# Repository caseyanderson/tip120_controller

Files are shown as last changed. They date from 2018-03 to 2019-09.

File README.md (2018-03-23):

# tip120_controller
Casey Anderson, 2018

## Overview

This repository provides `Printed Circuit Board` (`PCB`) files, as well as software examples, for an Arduino-based `TIP120` actuator controlled via `Potentiometer` (or any `Voltage Divider`). As described (in more detail) [here](http://bildr.org/2011/03/high-power-control-with-arduino-and-tip120/), the `TIP120` is capable of actuating a variety of devices including brushless DC motors, vibration motors, solenoids, and lightbulbs.

## PCB

This double-sided `Pin Through Hole` (`PTH`) PCB was created in EAGLE.

`VCC` is supplied to the `Arduino Mini` via `RAW` (12V maximum). `VCC` is also passed to the `T` pin of the `CONN JACK STEREO 3.5MM`. Connection to motors/solenoids/whatever is accomplished via 3.5mm audio cable. Rate of actuation is set via `Potentiometer` and passed to `Arduino Mini` via `A0`.

### BOM

Note: items without a `Manufacturer Part Number` are generic.

* 1x Arduino Pro Mini (3.3V, 8MHz)
* 1x SWITCH SLIDE SPDT 200MA 30V, `EG1218`
* 1x CONN PWR JACK 2X5.5MM SOLDER, `PJ-102A`
* 1x CONN JACK STEREO 3.5MM, `SJ1-3523N`
* 1x POT 10kR 1/20W CARBON LOG, `PTV09A-4020F-A103`
* 1x TIP120
* 1x 1N4004 Diode
* 1x 220R
* 1x 2.2kR
* 1x 5mm LED
* 1x Motor/Solenoid/Light

### Photo

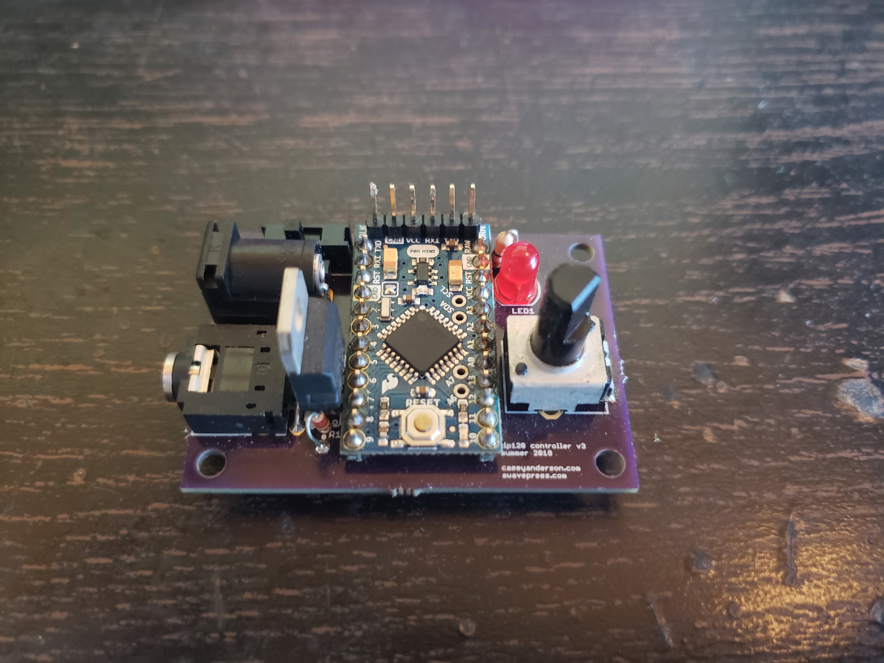
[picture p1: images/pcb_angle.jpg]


## SOFTWARE

Currently only the absolute simplest example of PWM. More to follow.

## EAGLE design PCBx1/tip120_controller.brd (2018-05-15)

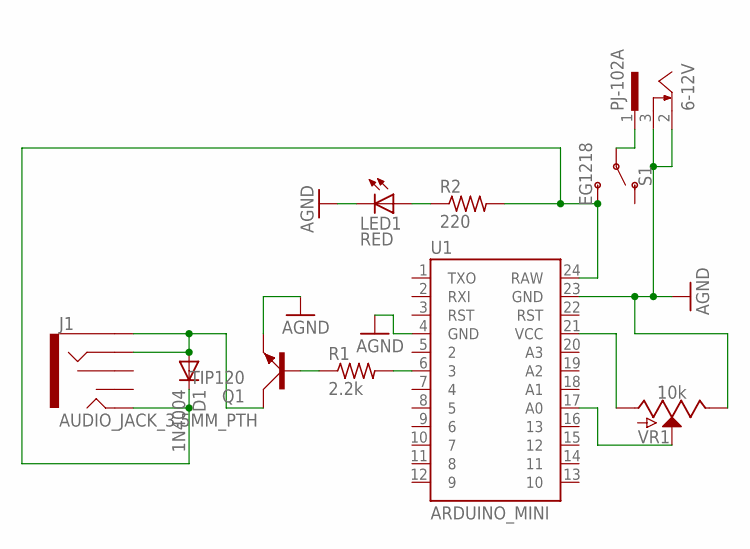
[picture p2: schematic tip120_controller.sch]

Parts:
D1: 1N4004; DO41-10
J1: AUDIO_JACK_3.5MM_PTH; AUDIO-JACK
LED1: RED; LED5MM
PJ-102A: 6-12V; SCD-014-A
Q1: TIP120; TO220AV
R1: 2.2k; 0204V
R2: 220; 0204V
S1: EG1218; SWITCH_SPDT_PTH_11.6X4.0MM_LOCK
U1: ARDUINO_MINI
VR1: 10k; POT-PTH-ALPS

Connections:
AGND: LED1.K (C), PJ-102A.2, PJ-102A.3, Q1.E, U1.4 (GND), U1.23 (GND), VR1.P$1 (E)
unnamed: R1.2, U1.6 (3)
unnamed: Q1.B, R1.1
unnamed: LED1.A, R2.1
unnamed: D1.A, J1.RING, J1.SLEEVE, Q1.C
unnamed: U1.21 (VCC), VR1.P$3 (A)
unnamed: U1.17 (A0), VR1.P$2 (S)
unnamed: PJ-102A.1, S1.2
unnamed: D1.C, J1.TIP, R2.2, S1.3 (S), U1.24 (RAW)

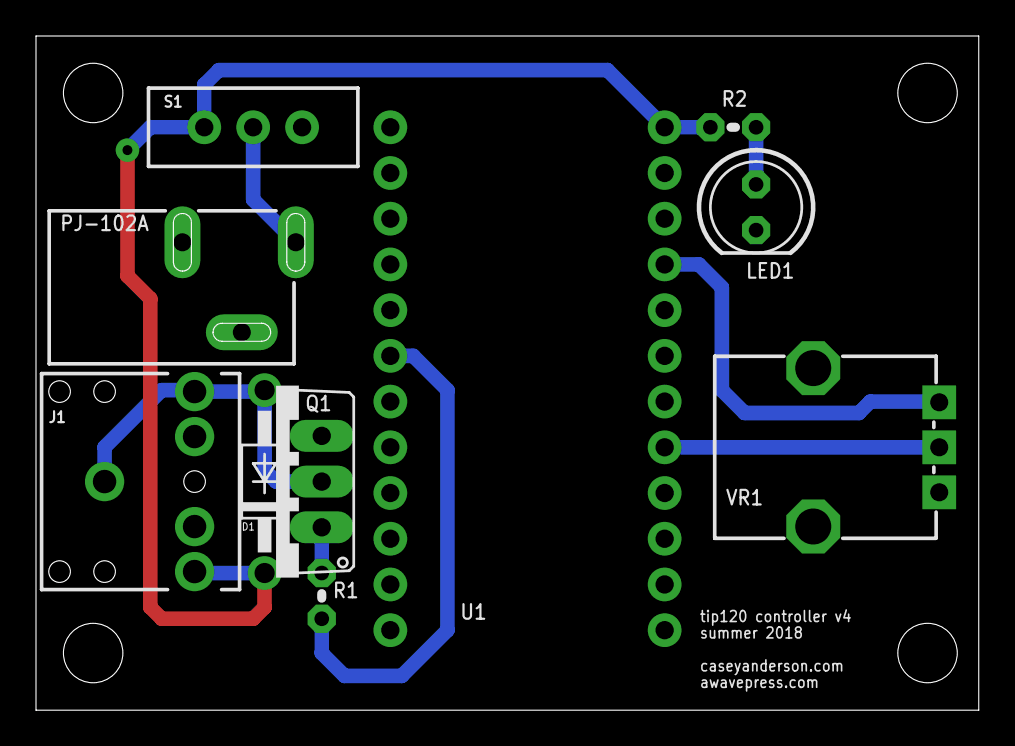
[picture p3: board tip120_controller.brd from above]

Board: 2 copper layers, 52.4 x 37.5 mm, 14 parts (0 on the bottom side), 9 nets.

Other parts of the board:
U$6, U$7, U$8, U$9: STAND-OFF

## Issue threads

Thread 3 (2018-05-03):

fix silkscreen ables

caseyanderson, 2018-05-03:

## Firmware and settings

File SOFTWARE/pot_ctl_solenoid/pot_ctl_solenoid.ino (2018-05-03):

/*
potentiometer sets rate of solenoid movement

code sourced from Arduino Help Message board (lost the url)

*/

const int PotPin = A0;
unsigned long cycleDuration; // total duration of one cycle (onTime+offTime)
unsigned long onTime = 50; // onTime within one cycle
unsigned long lastCycleStart;// start time of cycle

void setup() {
  pinMode(13, OUTPUT);
  pinMode(3, OUTPUT);

}

void loop() {
  // duration from onTime to onTime + 1023*20 milliseconds
  cycleDuration = onTime + analogRead(PotPin) * 20L; //  multiply with 'long' factor to make result long
  if (millis() - lastCycleStart >= cycleDuration)// time to start a new cycle
    lastCycleStart += cycleDuration; // remember time when cycle started
  digitalWrite(13, millis() - lastCycleStart < onTime); // LED HIGH during onTime
  digitalWrite(3, millis() - lastCycleStart < onTime); // VALVE HIGH during onTime
}

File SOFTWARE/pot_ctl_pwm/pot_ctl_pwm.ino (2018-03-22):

/*
  Pot sets PWM Value

*/

static const uint8_t analog_pin = A0;
static const uint8_t digital_pin = 3;

void setup() {
  Serial.begin(9600);

  pinMode(analog_pin, INPUT);
  pinMode( digital_pin, OUTPUT );

}

void loop() {
    unsigned int val = analogRead(analog_pin);
    analogWrite(digital_pin, val / 4);
  delay(2);
}

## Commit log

2018-03-22 the eagle files
    [tip120_controller.brd, tip120_controller.sch]
2018-03-22 simple pwm example
2018-03-24 solenoid with led
2018-05-03 added ground plane, moved led
    [tip120_controller.brd]
2018-05-04 moved via so its not under dc jack, layout is done
    [tip120_controller.brd]
2018-05-04 silkscreen update
    [tip120_controller.brd, tip120_controller.sch]
2018-05-04 replaced transistor symbol/footprint, futzing with silkscreen
    [tip120_controller.brd, tip120_controller.sch]
2018-05-04 sanity check
    [tip120_controller.brd, tip120_controller.sch]
2018-05-05 no labels for standoffs
    [tip120_controller.brd]
2018-05-15 swap footprints, update version number
    [tip120_controller.brd, tip120_controller.sch]
2018-05-15 reposition switch
    [tip120_controller.brd]
2019-09-08 updated photo with osh park pcb
    [tip120_controller.brd, tip120_controller.sch]

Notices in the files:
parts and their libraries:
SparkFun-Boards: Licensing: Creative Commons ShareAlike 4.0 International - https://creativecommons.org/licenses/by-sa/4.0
